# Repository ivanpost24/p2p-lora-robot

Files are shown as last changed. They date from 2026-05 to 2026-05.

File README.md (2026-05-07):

# WIoT final project

Authored by: Farjan Ahmed, Carlos Giron, Ivan Post

This is our final project for CS 4501: Wireless for the Internet of Things. It is a prototype system for controlling a mobile robot over long distances (from our observation, up to 0.32 km) using the LoRa physical layer protocol on Heltec ESP32 v3 LORA boards. It is designed to operate on the 915 MHz unlicensed band in the United States, which means you do not need an amateur radio license to use it. [This is a video of an operator controlling the robot from about 0.3 km away](https://drive.google.com/file/d/1XLk9izT9hsWHlGPpsFzeZ8Zzyy3jfpdS/view?usp=sharing); the control latency is primarily due to delays in the video feed and is under 500 ms in practice. The exact feasible range will depend on environmental factors.

We have provided instructions below to reproduce our prototype.

## Building the peripheral robot

### Components list:
* [WiFi LoRa 32 V3](https://heltec.org/project/wifi-lora-32-v3/) Heltec Board
* 2 [Sparkfun Dual tb6612fng Motor Drivers](https://www.sparkfun.com/sparkfun-motor-driver-dual-tb6612fng-1a.html) for motor control
* 4 [12V DC 100RPM Greartisan](amazon.com/Greartisan-Electric-Reduction-Centric-Diameter/dp/B072R57C56/ref=sr_1_6?crid=129Y1UB2Q6AGI&dib=eyJ2IjoiMSJ9.DwmBOBIYZeCSiQA5saHHIxj7DpqChe3S76xeKR8zBhYkiYd1JqMtlKpyXpX8ml9P-PodyTQpF1U53Aiup88Gdk4xNOoXEbOCuZ-eF9qleWwFV8hyrN2Rm18CDetzJ0f9fudnr4t8DZx4H_xdhjciGS_N9iVl0n4egDoUJzDH8lzn89O2e6Xu7hb-V0s1TQMCYfGA-40lgYDVYd1WclO5MOMkNcvgmsqaYL5KdbTtvnZBJRt6uXWlYDs0ATjglZvQkKjh9Chfi3PU3360LFzHv60yV7CS9oWNygZAhhukyWI.Be_9xpxrY9lM7WvLv97bnTWI3TeSQBAD8dNGXVNmA04&dib_tag=se&keywords=greartisan&qid=1778122489&sprefix=greara%2Caps%2C104&sr=8-6) Motors
* [INIU Portable Power Bank](https://www.amazon.com/INIU-Portable-Slimmest-Powerbank-Compatible/dp/B0DC9PV394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)
* [ACEIRMC USB Power Delivery Module](https://www.amazon.com/ACEIRMC-Trigger-Polling-Detector-Notebook/dp/B0BTHXKM91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) for requesting 12V from a power bank
* [HiLetgo game joystick](amazon.com/HiLetgo-Controller-JoyStick-Breakout-Arduino/dp/B00P7QBGD2)

Additional pcb relevant components such as resistors, switches, and connectors are shown in this schematic:
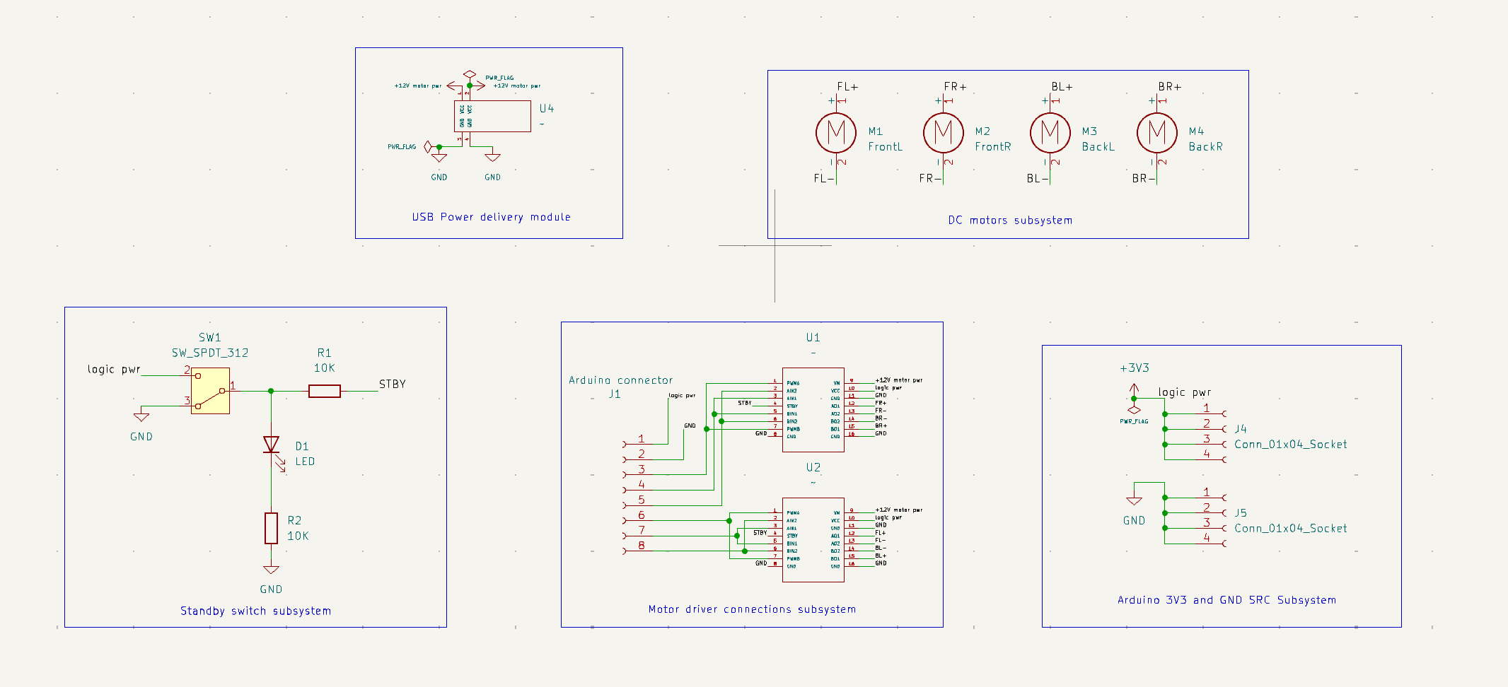
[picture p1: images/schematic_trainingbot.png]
robot schematic


The KiCad files for editing the schematic and gerbers for ordering PCBs are included in the "/KiCad" directory.

Mount the breakout boards for motor drivers and modules onto their respective locations on the pcb:
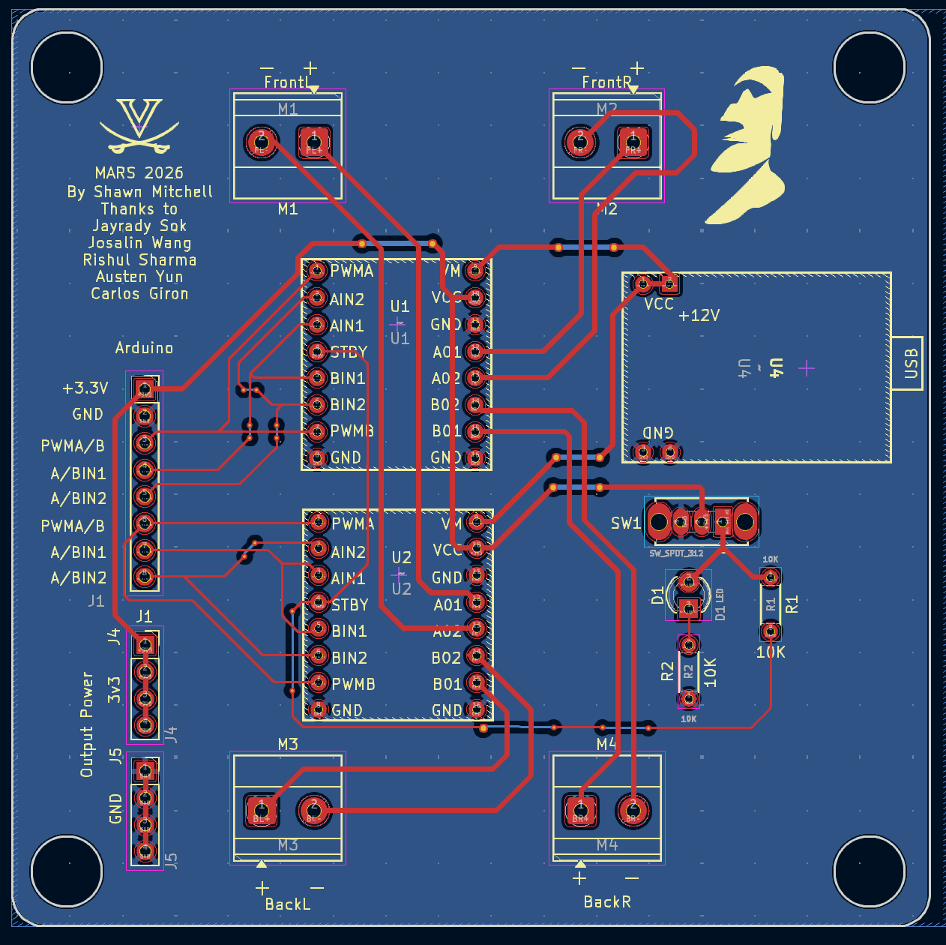
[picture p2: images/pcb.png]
robot pcb


## Building the central controller
### Pin assignments:
Assignments for the peripheral robot device are as follows:
* 19 - PWMA/B
* 20 - A/BIN1
* 26 - A/BIN2
* 47 - PWMA/B
* 48 - A/BIN1
* 33 - A/BIN2
* Connect external 3v3 supply and gnd

These pins are used to set the direction of motors and speed of motors as they are connected to tb6612fng motor drivers. You **MUST NOT** power the motor drivers using the 3v3 pins of the Heltec board. Due to a hardware issue it seems that these boards are unable to power the motor drivers and remain on for operation. You must use a seperate 3v3 source to power the drivers.

In our case we used an *Arduino Uno R3* to deliver 3v3, but a simple battery should suffice. It is important to remember to ground both Arduino and Heltec on the same rail otherwise reference issues for digital logic occur.

Assignments for the central controller are as follows:
* 7 - Vrx
* 6 - Vry
* 5 - Sw

Although the datasheet recommends using 5V as input, our code was designed around using 3v3.

## Deploying the provided code

This project uses PlatformIO, so configuring the project locally should be simple. Flash the Heltec v3 on the robot with the lora-peripheral code, and flash the Heltec v3 on the controller with the lora-central code. Everything should start automatically without any user input.

## Starting the robot
After code has been flashed onto the central and peripheral devices start the device as follows:
1. Connect the power delivery module to the power bank's 65 W output port
2. Connect the Arduino to the power bank
3. Connect the Heltec to the power bank
4. Flip the enable switch

If the PD module and onboard led are on then the robot is ready for operation if the devices were flashed successfully and connections were correct.

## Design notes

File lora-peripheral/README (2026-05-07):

# lora-peripheral

This is the robot's code. Flash this onto the Heltec v3 on the robot. The wiring of the robot is described below.

## Building the robot

...

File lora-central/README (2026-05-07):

# lora-central

This is the controller device's code. Flash this onto the Heltec v3 on the controller.

## Board description

...

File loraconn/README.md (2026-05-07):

# loraconn

Library providing data types for simple connection-style communication over LoRa. The full protocol specification is
provided below.

## 1. Physical layer

Devices shall use the LoRa communication standard. This should not be confused with LoRaWAN, which is the most popular
protocol using this physical layer protocol.

### 1.1. Channels

The protocol uses 32 channels in the 902-928 MHz ISM band numbered 0 to 31. Each channel has a bandwidth of 500 kHz,
and the spacing between each channel is 600 kHz. The frequency of channel $k$ can be calculated, in MHz, as follows:

    freq(k) = 908.4 + 0.6 * k

Channel 31 is reserved for advertising, and the remaining 30 channels are used for connections. Because the device is
transmitting at a bandwidth of 500 kHz, it is not necessary to hop channels, though this may be a nice feature to add
if the device is experiencing interference.

### 1.2. Data rate parameters

All transmissions shall use a coding rate of 4/5. The spreading factor shall be agreed upon in advance.

## 2. Data link layer

LoRaConn is designed specifically for communication between a pre-configured central and peripheral device. It is
assumed that the central device is relatively powerful and thus can supply its own power. The peripheral device is
assumed to be a relatively low-power device.

### 2.1. Base header

Every frame sent over this protocol begins with the following header. Devices shall use the protocol identifier to
filter irrelevant packets sent by devices using other protocols.

| Length | Name | Description |
| --- | --- | --- |
| 2 octets | Protocol identifier | 0x1195, which identifies the protocol. |
| 5 bits | Special | Special control flags, depending on the packet type. |
| 3 bits | Packet type | The type of the packet (see 2.1.1). |
| varies | Rest of frame | |

*Header length*: 3 octets

### 2.1.1. Packet types

The packet type field above may be one of the following. Each packet type is explained in further detail below.

| ID | Type |
| --- | --- |
| 000 | Advertisement |
| 001–010 | Reserved for future use |
| 011 | Connection request |
| 100 | Connection data |
| 101–110 | Reserved for future use |
| 111 | Disconnection request |

### 2.2. Advertising

The peripheral device shall periodically send out advertisements on channel 31. Central devices shall continuously
listen on channel 31 for advertisements. The central device is assumed to already know the device address of the
peripheral device to which it wishes to connect (this information is provided out-of-band).

Advertisements contain a peripheral device address and a requested RX window length for the central device, which
should be chosen based on the spreading factor and other encoding parameters.

| Length | Name | Description |
| --- | --- | --- |
| 6 octets | Peripheral device address | An uniquely identifying address for the peripheral device. |
| 2 octets | Central RX window | Time the central should wait after TX to the peripheral device for a response (little endian). |

*Data length:* 8 octets; *Total length*: 11 octets

### 2.3. Connection request

Once the central device receives an advertisement from the correct peripheral device, it shall send a connection
request in response as soon as possible. The connection request will contain a requested RX window length for the
peripheral device, which should be chosen based on the spreading factor and other encoding parameters.

#### 2.3.1. Connection request special section

| Bit index (LSB–MSB) | Name | Description |
| --- | --- | --- |
| 0–4 | Channel | The channel to use for communication, in the range \[0, 30\]. |

#### 2.3.2. Connection request main section

| Length | Name | Description |
| --- | --- | --- |
| 6 octets | Advertiser address | Address the advertiser used to identify itself. |
| 2 octets | Connection identifier | A randomly generated sequence to identify the connection. |
| 2 octets | Peripheral RX window  | Time the peripheral should wait after TX to the central device for a response (little endian). |
| 2 octets | Window offset | Time the peripheral should wait after receiving this request until the first RX window (little endian). |

*Data length*: 12 octets; *Total length*: 15 octets

### 2.4. Connection data

Once a connection request is sent, the central device will send the first packet of the connection after the provided
window offset time, measured from the end of the packet transmission.

| Length | Name | Description |
| --- | --- | --- |
| 2 octets | Connection identifier | The same connection identifier sent in the connection request. |
| varies | Payload | |

*Header length:* 2 octets; *Total length*: at least 5 octets.

### 2.5. Disconnection request

Either device may send a disconnection request to terminate the connection.

| Length | Name | Description |
| --- | --- | --- |
| 2 octets | Connection identifier | The same connection identifier sent in the connection request. |

*Data length:* 2 octets; *Total length*: 5 octets

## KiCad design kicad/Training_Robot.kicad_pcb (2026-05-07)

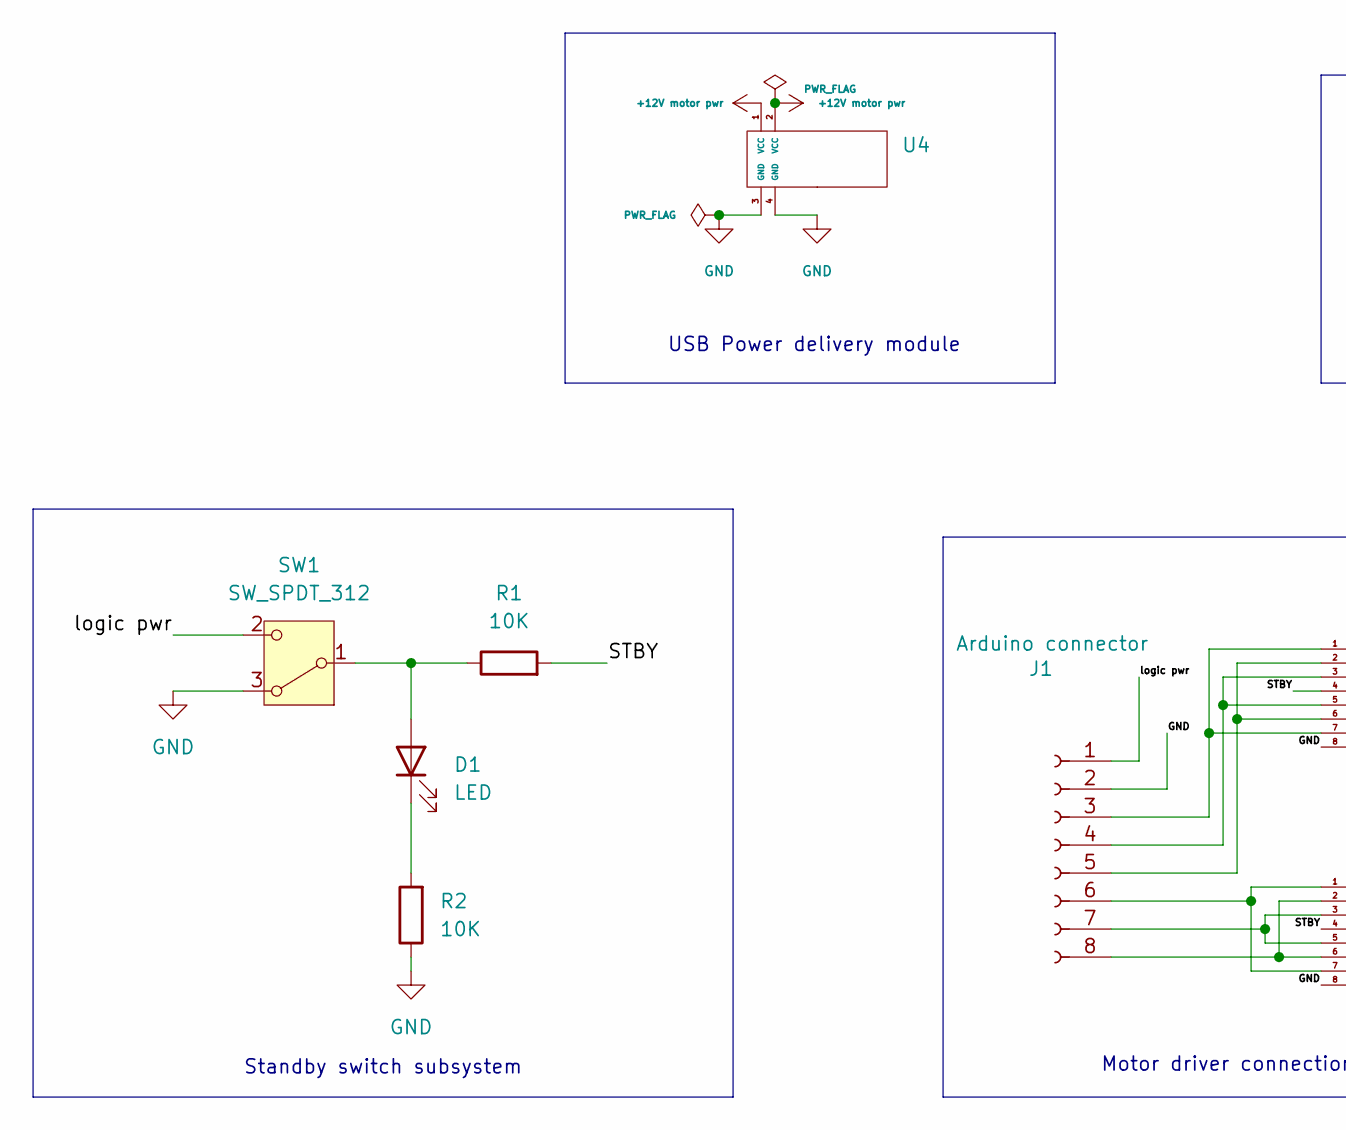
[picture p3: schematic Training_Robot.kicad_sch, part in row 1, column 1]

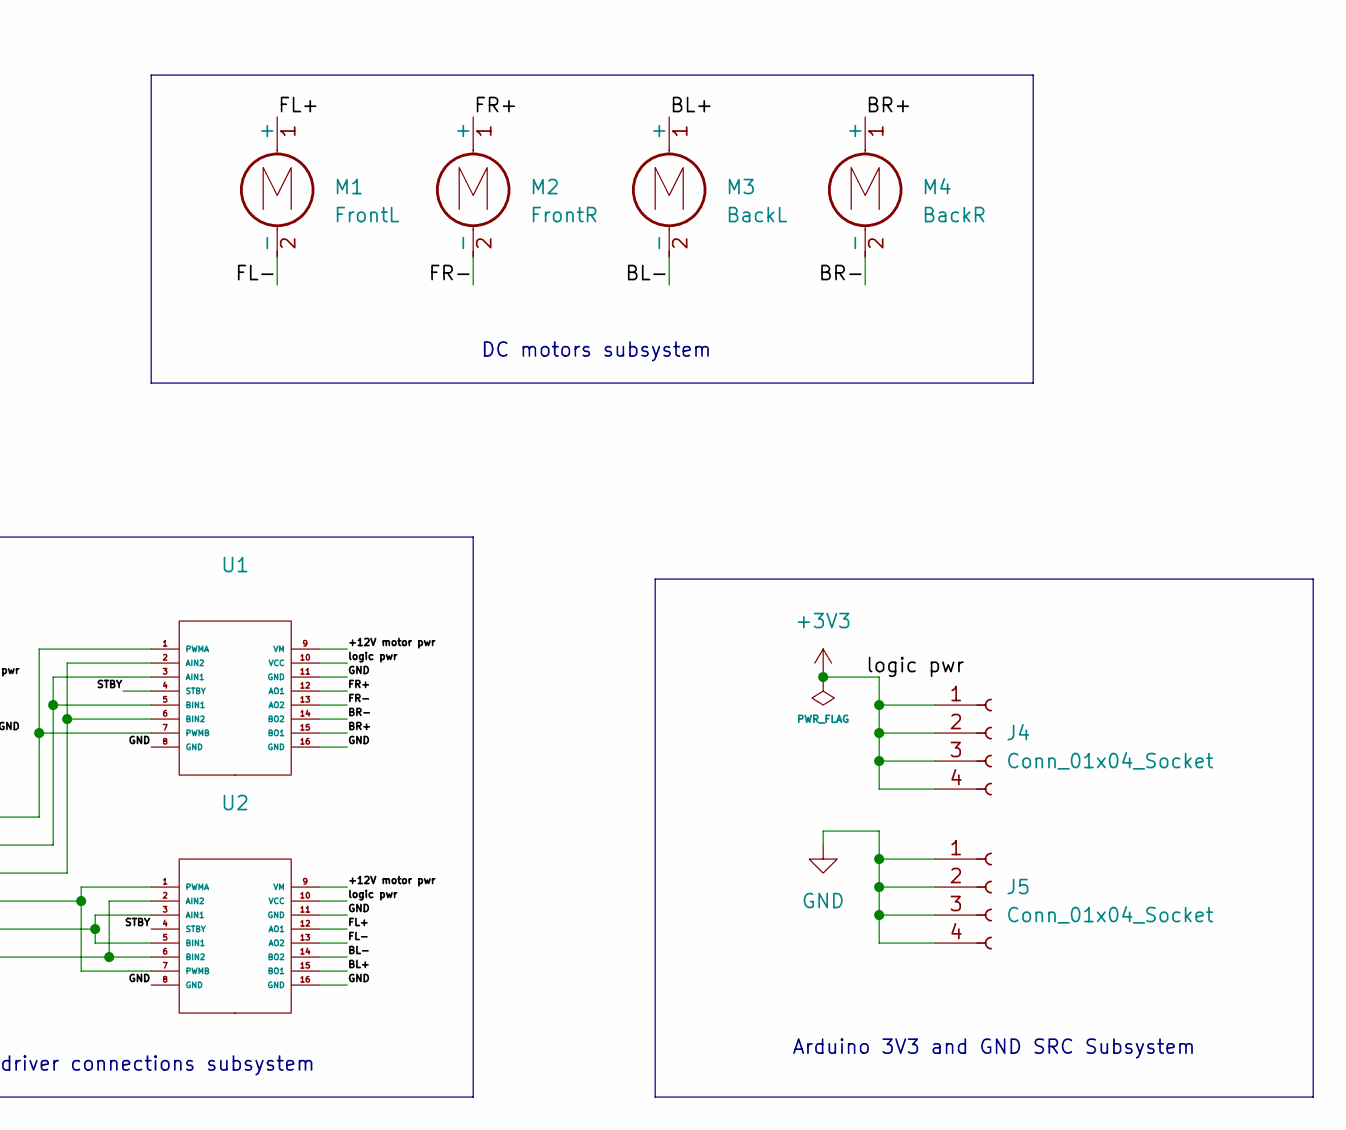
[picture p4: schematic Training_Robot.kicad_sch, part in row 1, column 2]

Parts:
D1: LED; LED_D3.0mm
J1: Arduino connector; PinSocket_1x08_P2.54mm_Vertical
J4, J5: Conn_01x04_Socket; PinSocket_1x04_P2.54mm_Vertical
M1: FrontL; TerminalBlock_Phoenix_MKDS-1,5-2_1x02_P5.00mm_Horizontal
M2: FrontR; TerminalBlock_Phoenix_MKDS-1,5-2_1x02_P5.00mm_Horizontal
M3: BackL; TerminalBlock_Phoenix_MKDS-1,5-2_1x02_P5.00mm_Horizontal
M4: BackR; TerminalBlock_Phoenix_MKDS-1,5-2_1x02_P5.00mm_Horizontal
R1, R2: 10K; R_Axial_DIN0204_L3.6mm_D1.6mm_P5.08mm_Horizontal
SW1: SW_SPDT_312; SW_Slide_SPDT_Straight_CK_OS102011MS2Q
U1, U2: TB_breakout_motor_driver
U4: PD Module

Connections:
+3V3: J1.1, J4.1, J4.2, J4.3, J4.4, SW1.2 (C), U1.10 (VCC), U2.10 (VCC)
+12V motor pwr: U1.9 (VM), U2.9 (VM), U4.1 (VCC), U4.2 (VCC)
/BL+: M3.1 (+), U2.15 (BO1)
/BL-: M3.2 (-), U2.14 (BO2)
/BR+: M4.1 (+), U1.15 (BO1)
/BR-: M4.2 (-), U1.14 (BO2)
/FL+: M1.1 (+), U2.12 (AO1)
/FL-: M1.2 (-), U2.13 (AO2)
/FR+: M2.1 (+), U1.12 (AO1)
/FR-: M2.2 (-), U1.13 (AO2)
/STBY: R1.2, U1.4 (STBY), U2.4 (STBY)
GND: J1.2, J5.1, J5.2, J5.3, J5.4, R2.1, SW1.3 (A), U1.8 (GND), U1.11 (GND), U1.16 (GND), U2.8 (GND), U2.11 (GND), U2.16 (GND), U4.3 (GND), U4.4 (GND)
unnamed: D1.2 (A), R1.1, SW1.1 (B)
unnamed: D1.1 (K), R2.2
unnamed: J1.3, U1.1 (PWMA), U1.7 (PWMB)
unnamed: J1.4, U1.3 (AIN1), U1.5 (BIN1)
unnamed: J1.5, U1.2 (AIN2), U1.6 (BIN2)
unnamed: J1.6, U2.1 (PWMA), U2.7 (PWMB)
unnamed: J1.7, U2.3 (AIN1), U2.5 (BIN1)
unnamed: J1.8, U2.2 (AIN2), U2.6 (BIN2)

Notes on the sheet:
DC motors subsystem
Standby switch subsystem
USB Power delivery module
Arduino 3V3 and GND SRC Subsystem
Motor driver connections subsystem

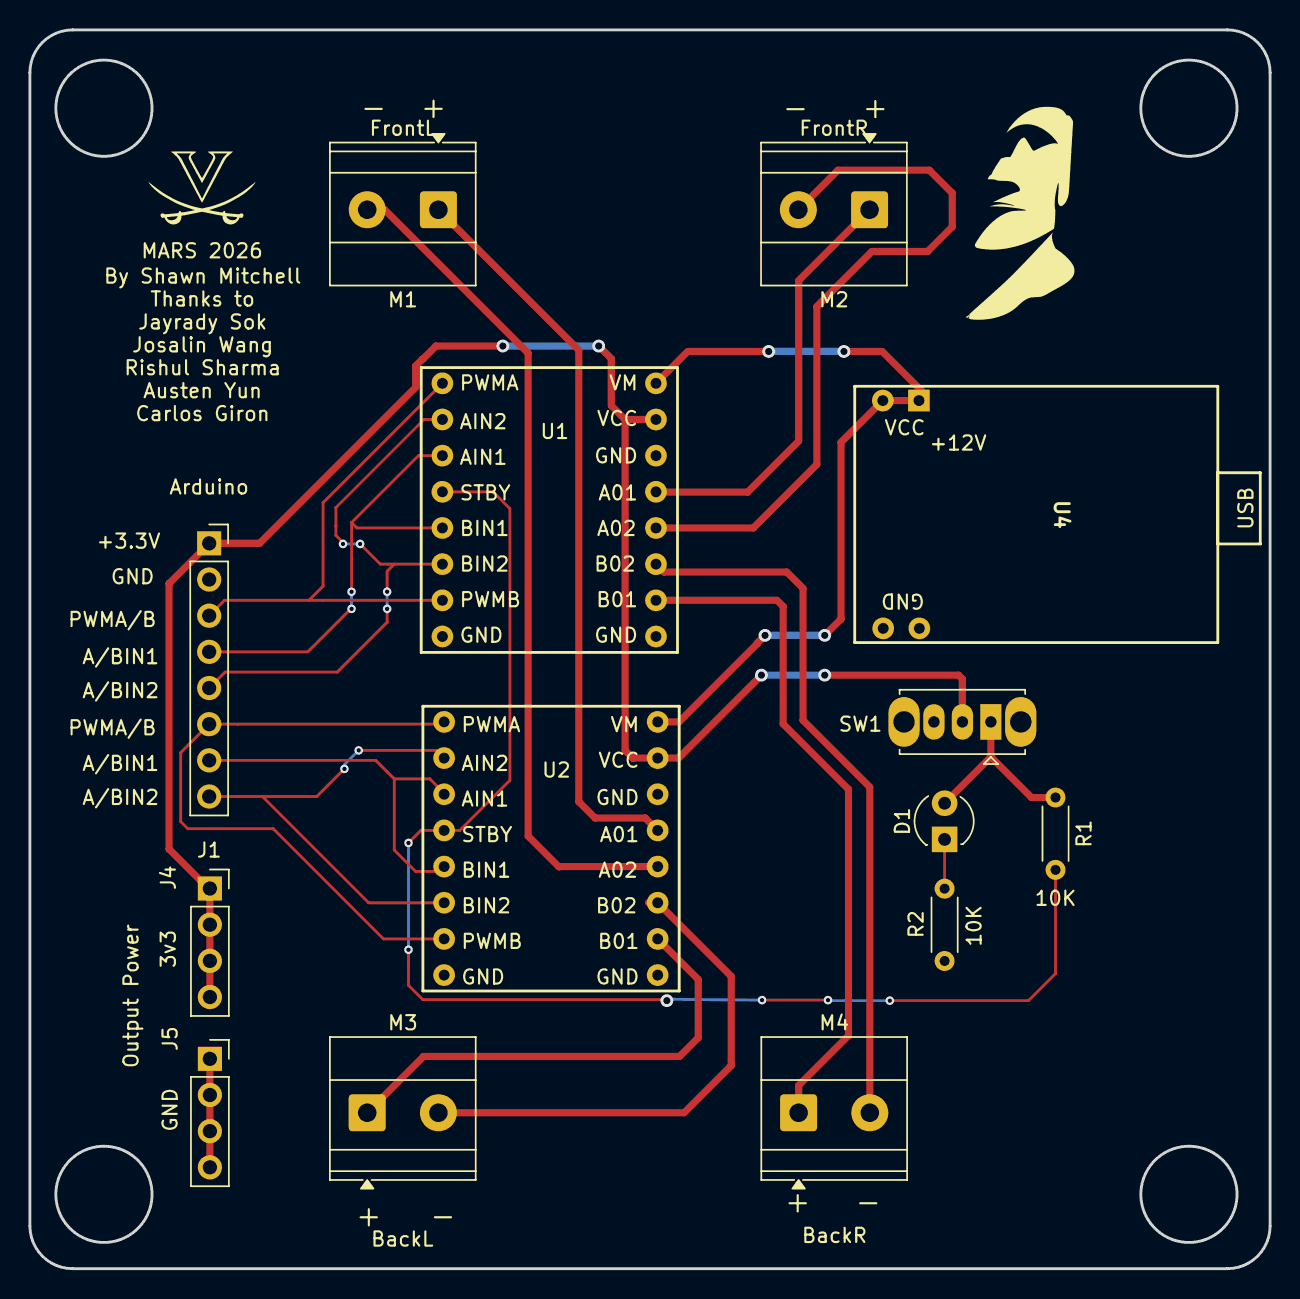
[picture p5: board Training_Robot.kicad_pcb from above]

Board: 2 copper layers, 87.1 x 87.0 mm, 14 parts (0 on the bottom side), 20 nets.

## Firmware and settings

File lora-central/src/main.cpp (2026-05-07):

/*
To successfully receive data, the following settings have to be the same
on both transmitter and receiver:
- carrier frequency
- bandwidth
- spreading factor
*/

// include the library
#include <RadioLib.h>
#include "loraconn.hpp"

/// @brief Perform additional setup after the radio has been configured.
///
/// This function is called at the end of the Arduino `setup()` function after
/// the radio has been configured.
extern void performSetup();

/// @brief Prepare to initiate a connection with the peripheral device.
///
/// This function is called right before transmitting a connection request.
/// Return 0 at the end of the function to continue connecting. If you
/// return another value instead, the device will not attempt to connect.
/// @return `0` if you wish to continue connecting, and a different if you wish
///     to not attempt to connect.
extern int onPeripheralDetected();

/// @brief Prepare the next packet for transmission.
///
/// This function is called right before transmitting a packet. It should
/// modify the provided buffer and length for the data you wish to transmit.
/// Return 0 at the end of the function to perform a transmission. If you
/// return another value instead, the device will terminate the connection.
/// @param data Output buffer which will contain the data you wish to transmit.
/// @param capacity Capacity of the output buffer.
/// @param len Length of the output buffer.
/// @return `0` if you wish to continue the connection, and a different value
///     if you wish to terminate it.
extern int prepareTxPacket(uint8_t *data, uint8_t capacity, uint8_t& len);

/// @brief Process a received packet.
///
/// This function is called right after receiving a packet and provides the received
/// data as input. Return true at the end of the function to indicate that the device
/// should stop listening for data (because the received data is valid). Return false to
/// ask the device to continue listening until timeout.
/// @param data Input buffer which contains the data received.
/// @param len Length of the input buffer.
/// @return `0` if you want the device to stop listening and switch to transmission,
///     another value if you want the device to continue listening.
extern int onReceive(const uint8_t *data, uint8_t len);

/**************** Pin assignment for the Heltec V3 board ******************/
static constexpr int LORA_CS    = 8;      // Chip select pin
static constexpr int LORA_MOSI  = 10;
static constexpr int LORA_MISO  = 11;
static constexpr int LORA_SCK   = 9;
static constexpr int LORA_NRST  = 12;      // Reset pin
static constexpr int LORA_DIO1  = 14;      // DIO1 switch
static constexpr int LORA_BUSY  = 13;
static constexpr int BUTTON     = 0;

/****************LoRa parameters (you need to fill these params)******************/
static constexpr uint8_t SF = 10;
static constexpr int8_t TX_PWR = 22;
static constexpr uint8_t CR = 5;
static constexpr uint8_t SYNC_WORD = (uint8_t)0x34;
static constexpr uint16_t PREAMBLE = 8;

static constexpr loraconn::MACAddress peripheralAddress = {0x58, 0x02, 0x34, 0x00, 0xfe, 0x54};
static constexpr unsigned long connWindowOffset = 150000;
static constexpr unsigned long peripheralRxWindow = 150000;
static constexpr unsigned long txDelay = 500;
static constexpr uint8_t missedPacketsTolerance = 4;

enum class State
{
    IDLE,
    SCAN_TX,
    SCAN_RX,
    CONN_STARTING,
    CONN_TX,
    CONN_RX,
    CONN_TX_SLEEP,
    DISCONN_TX,
};

static volatile State state(State::IDLE);
static volatile bool operationCompleted = false;
static volatile uint16_t txError = RADIOLIB_ERR_NONE;
static volatile uint8_t channel = loraconn::ADVERTISING_CHANNEL;
static volatile unsigned long rxWindow = 0;
static volatile unsigned long eventStart = 0;
static loraconn::ConnectionIdentifier connId;
static uint8_t buf[255];
static loraconn::Packet packet(255);
static loraconn::ConnectionData txData(249);
static uint8_t missedPackets = 0;

// this function is called when a complete packet
// is received by the module
// IMPORTANT: this function MUST be 'void' type
//            and MUST NOT have any arguments!
#if defined(ESP8266) || defined(ESP32)
ICACHE_RAM_ATTR
#endif
void onOperationCompleted(void)
{
    operationCompleted = true;
}

void sendError(const char* message, int16_t state)
{
    Serial.printf("ERROR: %s (error code %d).\n", message, state);
}

// Helper function to print error messages
void terminateWithError(const char* message, int16_t state)
{
    Serial.printf("ERROR: %s (error code %d). Terminating.\n", message, state);
    while(true); // loop forever
}

SX1262 radio = new Module(LORA_CS, LORA_DIO1, LORA_NRST, LORA_BUSY);

static uint16_t tune(uint8_t channel)
{
    int err;
    err = radio.setFrequency(loraconn::getChannelFrequency(channel));
    if (err != RADIOLIB_ERR_NONE) {
        Serial.print(F("Error tuning radio to channel "));
        Serial.print(channel);
        Serial.printf(" (error code %d)\n", err);
        return err;
    }

    err = radio.setBandwidth(loraconn::getChannelBandwidth(channel));
    if (err != RADIOLIB_ERR_NONE) {
        Serial.print(F("Error setting radio bandwidth (error code "));
        Serial.printf(" (error code %d)\n", err);
        return err;
    }

    Serial.print(F("Changed channel to "));
    Serial.println(channel);
    return RADIOLIB_ERR_NONE;
}

static uint16_t startTransmitting(const loraconn::Packet& packet)
{
    return radio.startTransmit(packet.getRaw(), packet.getLength());
}

static bool readPacket(loraconn::Packet& out) {
    size_t length = radio.getPacketLength();
    if (length > 255) {
        sendError("Read packet was too long", RADIOLIB_ERR_PACKET_TOO_LONG);
        return false;
    }
    int err = radio.readData(buf, length);
    if (err != RADIOLIB_ERR_NONE) {
        sendError("Failed to receive packet", err);
        return false;
    } else if (!out.setRaw(buf, length)) {
        Serial.println(F("Ignoring non-LoRaConn packet"));
        return false;
    } else {
        return true;
    }
}

static bool currentlyReceivingPacket() {
    uint32_t flags = radio.getIrqFlags();
    return flags == RADIOLIB_IRQ_PREAMBLE_DETECTED || flags == RADIOLIB_IRQ_RX_DONE;
}

void setup()
{
    Serial.begin(115200);

    // initialize SX1262 with default settings
    Serial.print(F("[SX1262] Initializing ... "));
    int err = radio.begin();
    if (err == RADIOLIB_ERR_NONE) {
        Serial.println(F("success!"));
    } else {
        terminateWithError("Failed to start radio", err);
    }

    err = radio.setSpreadingFactor(SF);
    if (err != RADIOLIB_ERR_NONE) {
        terminateWithError("SF initialization failed", err);
    }
    Serial.print("[SX1262] Spreading Factor:\t\t");
    Serial.println(SF);
    err = radio.setOutputPower(TX_PWR);
    if (err != RADIOLIB_ERR_NONE) {
        terminateWithError("Output Power initialization failed", err);
    }
    Serial.print("[SX1262] Transmit Power:\t\t");
    Serial.print(TX_PWR);
    Serial.println(F(" dBm"));

    err = radio.setCurrentLimit(140.0);
    if (err != RADIOLIB_ERR_NONE) {
        terminateWithError("Current limit intialization failed", err);
    }
    radio.setDio1Action(onOperationCompleted);

    performSetup();
}

void loop(void)
{
    uint16_t err;
    switch (state) {
    case State::IDLE:
        tune(loraconn::ADVERTISING_CHANNEL);
        state = State::SCAN_RX;
        err = radio.startReceive();
        if (err == RADIOLIB_ERR_NONE) {
            Serial.print(F("Waiting for advertisement ... "));
        } else {
            sendError("Failed to start receiving", err);
            state = State::IDLE;
        }
        return;
    case State::SCAN_TX:
        if (operationCompleted) {
            operationCompleted = false;
            if (txError == RADIOLIB_ERR_NONE) {
                Serial.println(F("success"));
            } else {
                sendError("failed", txError);
            }
            state = State::CONN_STARTING;
            eventStart = micros();
        }
        return;
    case State::SCAN_RX:
        if (operationCompleted) {
            operationCompleted = false;
            if (readPacket(packet)) {
                if (packet.getPacketType() == loraconn::PacketType::ADVERT) {
                    loraconn::Advertisement advertisement(packet);
                    if (advertisement.advertiserAddressMatches(peripheralAddress)) {
                        Serial.println(F("Found peripheral device!"));
                        eventStart = micros();
                        err = radio.finishReceive();
                        operationCompleted = false;
                        if (err != RADIOLIB_ERR_NONE) {
                            sendError("Failed to finish receiving", err);
                        }
                        err = onPeripheralDetected();
                        if (err == 0) {
                            rxWindow = static_cast<unsigned long>(advertisement.getCentralRxWindow()) * 100;
                            long randomId = random();
                            connId.at(0) = (randomId >> 8) & 0xff;
                            connId.at(1) = randomId & 0xff;
                            do {
                                channel = random() & 0b11111;
                            } while (channel == 31);
                            loraconn::ConnectionRequest connRequest;
                            connRequest.setAdvertiserAddress(peripheralAddress);
                            connRequest.setChannel(channel);
                            connRequest.setConnectionIdentifier(connId);
                            connRequest.setWindowOffset(static_cast<uint16_t>(connWindowOffset / 100));
                            connRequest.setPeripheralRxWindow(static_cast<uint16_t>(peripheralRxWindow / 100));

                            state = State::SCAN_TX;
                            txError = startTransmitting(connRequest);
                            Serial.print(F("Starting connection request ... "));
                        } else {
                            sendError("Not attempting to connect", err);
                            state = State::IDLE;
                        }
                    } else {
                        Serial.println(F("Ignoring advertisement from incorrect device"));
                    }
                } else {
                    Serial.println(F("Ignoring packet of incorrect type"));
                }
            } else {
                Serial.println(F("Ignoring packet of incorrect protocol"));
            }
        }
        return;
    case State::CONN_STARTING:
        if (micros() - eventStart >= connWindowOffset) {
            err = tune(channel);
            if (err == RADIOLIB_ERR_NONE) {
                state = State::CONN_TX_SLEEP;
                eventStart = micros();
            } else {
                state = State::IDLE;
            }
        }
        return;
    case State::CONN_TX:
        if (operationCompleted) {
            operationCompleted = false;
            if (txError == RADIOLIB_ERR_NONE) {
                Serial.println(F("success"));
            } else {
                sendError("failed", txError);
            }
            state = State::CONN_RX;
            err = radio.startReceive();
            if (err == RADIOLIB_ERR_NONE) {
                Serial.print(F("Waiting for next packet ... "));
            } else {
                sendError("Failed to start receiving", err);
                state = State::IDLE;
            }
            eventStart = micros();
        }
        return;
    case State::CONN_RX:
        if (operationCompleted) {
            operationCompleted = false;
            if (readPacket(packet)) {
                if (packet.getPacketType() == loraconn::PacketType::CONN_DATA) {
                    loraconn::ConnectionData connData(packet);
                    if (connData.connectionIdentifierMatches(connId)) {
                        uint8_t length = connData.getPayloadLength();
                        uint8_t payload[length];
                        connData.getPayload(payload);
                        err = onReceive(payload, length);
                        if (err == 0) {
                            err = radio.finishReceive();
                            operationCompleted = false;
                            missedPackets = 0;
                            if (err != RADIOLIB_ERR_NONE) {
                                sendError("Failed to finish receiving", err);
                            }
                            state = State::CONN_TX_SLEEP;
                            eventStart = micros();
                        } else {
                            sendError("Invalid connection data payload", err);
                        }
                    } else {
                        Serial.println(F("Ignoring data from a different connection"));
                    }
                } else if (packet.getPacketType() == loraconn::PacketType::DISCONN_REQ) {
                    loraconn::DisconnectionRequest disconnRequest(packet);
                    if (disconnRequest.connectionIdentifierMatches(connId)) {
                        Serial.println("Disconnecting");
                        state = State::IDLE;
                    } else {
                        Serial.println(F("Ignoring data from a different connection"));
                    }
                } else {
                    Serial.println(F("Ignoring packet of an incorrect type"));
                }
            } else {
                Serial.println(F("Ignoring packet of incorrect protocol"));
            }
        } else if (micros() - eventStart >= rxWindow && !currentlyReceivingPacket()) {
            Serial.println(F("Missed packet"));
            if (++missedPackets > missedPacketsTolerance) {
                Serial.println(F("Disconnecting"));
                state = State::IDLE;
            } else {
                state = State::CONN_TX_SLEEP;
            }
        }
        return;
    case State::CONN_TX_SLEEP:
        if (micros() - eventStart >= txDelay) {
            txData.setConnectionIdentifier(connId);
            uint8_t length;
            err = prepareTxPacket(txData.payload(), 249, length);
            if (err == 0) {
                state = State::CONN_TX;
                txData.setPayloadLength(length);
                eventStart = micros();
                txError = startTransmitting(txData);
                Serial.print(F("Started transmitting ... "));
            } else {
                state = State::DISCONN_TX;
                loraconn::DisconnectionRequest disconnRequest;
                disconnRequest.setConnectionIdentifier(connId);
                eventStart = micros();
                txError = startTransmitting(disconnRequest);
                Serial.print(F("Disconnecting ... "));
            }
        }
        return;
    case State::DISCONN_TX:
        if (operationCompleted) {
            operationCompleted = false;
            if (txError == RADIOLIB_ERR_NONE) {
                Serial.println(F("success"));
            } else {
                sendError("failed", txError);
            }

            state = State::IDLE;
        }
        return;
    default:
        Serial.println("Invalid state");
        while (true);
    }
}

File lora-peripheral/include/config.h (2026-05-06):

#pragma once

// ============================================================
// config.h — pin assignments and tuning constants
//
// SCHEMATIC NOTES (training-robot-schem):
//   U1 = RIGHT side motors (FR+, FR-, BR+, BR-)
//   U2 = LEFT  side motors (FL+, FL-, BL+, BL-)
//
//   STBY is driven by physical switch SW1 (10K pulldown + LED
//   indicator). J1-4 also connects to this net, so GPIO can
//   pull STBY LOW for e-stop — but SW1 must be ON for GPIO
//   to be able to bring STBY HIGH. Both must agree.
//
// PIN VERIFICATION CHECKLIST:
//   Before first motor test, verify with a multimeter that
//   each Heltec GPIO actually reaches the correct TB6612 pin.
//   The assignments below are from the hardware brief and may
//   need adjustment based on your actual jumper wiring.
// ============================================================

// ------------------------------------------------------------
// TB6612FNG — U1 (RIGHT side: FR, BR motors)
// Schematic: U1 AO1=FR+  AO2=FR-  BO1=BR+  BO2=BR-
// ------------------------------------------------------------
#define PIN_PWMR   19   // U1 PWMA  — right speed
#define PIN_RIN1   33   // U1 AIN1  — right forward
#define PIN_RIN2   20   // U1 AIN2  — right backward
                        // ⚠ GPIO21 also = OLED RST on Heltec V3 PCB
                        //   Fine for motor-only test, remap (35/36)
                        //   before combining with OLED code

// ------------------------------------------------------------
// TB6612FNG — U2 (LEFT side: FL, BL motors)
// Schematic: U2 AO1=FL+  AO2=FL-  BO1=BL+  BO2=BL-
// ------------------------------------------------------------
#define PIN_PWML   26   // U2 PWMA  — left speed  (PWMA on U2, not PWMB)
#define PIN_LIN1   48   // U2 AIN1  — left forward
#define PIN_LIN2   47   // U2 AIN2  — left backward

// ------------------------------------------------------------
// STBY — shared net, both chips
// Schematic: SW1 physical switch also on this net.
//   SW1 must be in ON position for GPIO to assert HIGH.
//   GPIO pulling LOW always wins (e-stop still works).
// ------------------------------------------------------------

// ------------------------------------------------------------
// KY-023 Joystick — power from 3.3V pin (NOT VUSB/5V)
// ADC max is 3.3V; powering from 5V would damage ADC inputs.
// ------------------------------------------------------------
#define PIN_VRX    7    // ADC1_CH6 — safe analog input
#define PIN_VRY    6    // ADC1_CH5 — safe analog input
#define PIN_SW     5   //

// ------------------------------------------------------------
// HC-SR04 Ultrasonic — stubbed, implement later
// ------------------------------------------------------------
#define PIN_TRIG   10
#define PIN_ECHO   11
#define SONAR_MAX_CM 200

// ------------------------------------------------------------
// LEDC (PWM) — ESP32-S3 hardware PWM peripheral
// TB6612 max PWM freq: 100 kHz. 1 kHz is safe and inaudible.
// 8-bit resolution → duty 0–255.
// ------------------------------------------------------------
#define LEDC_CH_LEFT    0
#define LEDC_CH_RIGHT   1
#define LEDC_FREQ_HZ    1000
#define LEDC_RES_BITS   8

// ------------------------------------------------------------
// Joystick ADC tuning
// ADC_CENTER: 12-bit midpoint. KY-023 at 3.3V → center ≈ 2048.
// ADC_DEADZONE: raw counts either side of center treated as zero.
//   80 counts ≈ 64 mV — covers pot noise and mechanical slop.
// ------------------------------------------------------------
#define ADC_CENTER    2024 // 1024
#define ADC_DEADZONE    120 //  80

// ------------------------------------------------------------
// Motor test sequence (used in startup verification)
// ------------------------------------------------------------
#define TEST_DUTY       150   // PWM duty for startup test (0-255)
#define TEST_DURATION_MS 400  // how long each test pulse runs

// ------------------------------------------------------------
// Control loop timing
// ------------------------------------------------------------
#define LOOP_PERIOD_MS   20   // 50 Hz

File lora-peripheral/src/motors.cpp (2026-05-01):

#include "motors.h"
#include "config.h"

// ============================================================
// motors.cpp — TB6612FNG + LEDC implementation
// ============================================================

// ------------------------------------------------------------
// Internal helper — set one TB6612 channel
//
// TB6612 truth table (active drive mode):
//   IN1  IN2   Motor output
//    H    L    Forward
//    L    H    Reverse
//    L    L    Coast (both outputs hi-Z)
//    H    H    Brake (both outputs pulled to GND) — avoid,
//              causes shoot-through on the H-bridge
// ------------------------------------------------------------
static void _set_channel(int8_t speed, uint8_t ledc_ch,
                          uint8_t pin_fwd, uint8_t pin_rev) {
    if (speed == 0) {
        digitalWrite(pin_fwd, LOW);
        digitalWrite(pin_rev, LOW);
        ledcWrite(ledc_ch, 0);
        return;
    }

    if (speed > 0) {
        digitalWrite(pin_fwd, HIGH);
        digitalWrite(pin_rev, LOW);
    } else {
        digitalWrite(pin_fwd, LOW);
        digitalWrite(pin_rev, HIGH);
        speed = -speed;
    }

    ledcWrite(ledc_ch, (uint8_t)speed);
}

// ------------------------------------------------------------
// Public API
// ------------------------------------------------------------

void motors_init() {
    pinMode(PIN_RIN1, OUTPUT);
    pinMode(PIN_RIN2, OUTPUT);
    pinMode(PIN_LIN1, OUTPUT);
    pinMode(PIN_LIN2, OUTPUT);

    ledcSetup(LEDC_CH_LEFT,  LEDC_FREQ_HZ, LEDC_RES_BITS);
    ledcSetup(LEDC_CH_RIGHT, LEDC_FREQ_HZ, LEDC_RES_BITS);
    ledcAttachPin(PIN_PWMR, LEDC_CH_LEFT);
    ledcAttachPin(PIN_PWML, LEDC_CH_RIGHT);

    motors_stop();
}

void motor_left(int8_t speed) {
    _set_channel(speed, LEDC_CH_LEFT, PIN_LIN1, PIN_LIN2);
}

void motor_right(int8_t speed) {
    _set_channel(speed, LEDC_CH_RIGHT, PIN_RIN1, PIN_RIN2);
}

void motors_stop() {
    motor_left(0);
    motor_right(0);
}

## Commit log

2026-04-28 Fix a few issues
    [loraconn.hpp]
2026-04-28 Added packet type assertions in conversion constructors (to prevent accidental conversions)
    [loraconn.hpp]
2026-04-30 First attempt at central device counter (untested)
2026-05-01 Changed protocol to achieve TDMA with alternating RX windows instead of time slots
2026-05-01 Add missing performSetup() declaration and usage in main for lora-central
    [main.cpp]
2026-05-01 fixed bounds and mem usage for joystick
    [joystick.cpp, motors.cpp]
2026-05-06 Increased spreading factor to 10 and TX power to 22 dB
2026-05-07 Added more tolerance for missed packets
    [main.cpp]
2026-05-07 Added motor command message for better debugging
2026-05-07 added images and gerbers for pcb
    [Training_Robot-B_Cu.gbr, Training_Robot-B_Mask.gbr, Training_Robot-B_Silkscreen.gbr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]
